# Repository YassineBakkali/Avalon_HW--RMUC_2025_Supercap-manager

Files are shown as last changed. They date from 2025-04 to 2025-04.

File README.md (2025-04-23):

# Avalon - A supercapacitor power manager 

**Avalon** is the custom-designed supercapacitor power manager developed by the **Calibur Robotics team at the National University of Singapore (NUS)** for the **RoboMaster University Championship 2025 (RMUC)**.

This repository contains the full KiCad design files for the Avalon PCB, along with exported schematics and layout PDFs for easier reference and review. Avalon is built to manage high-speed charge and discharge cycles between the robot’s main power source and a dedicated supercapacitor bank.

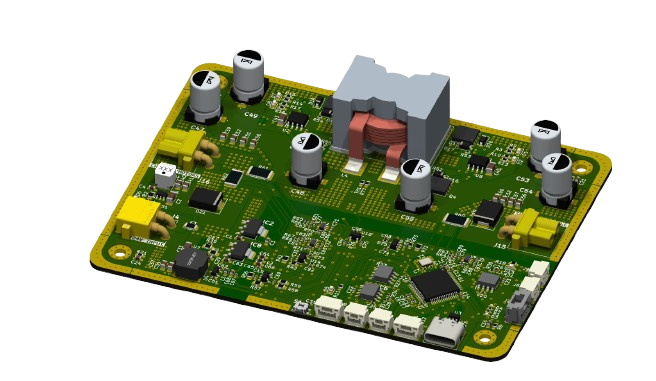
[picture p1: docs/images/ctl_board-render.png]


## Overview

In the RoboMaster competitions, robots must obey strict power limits enforced by the referee system -- typicallycapping the power that can be drawn by the chassis motors at any time. However, short bursts of movement like sprints, collisions, or sudden maneuvers demand far more power than the allowed continuous limit. This creates a mismatch between what the robot can legally draw and what it momentarily needs.

This supercapacitor charger board acts as an intelligent power managemennt module that bridges that gap. By interfacing between the robot's power input (PMM) and supercapacitor bank, it performs real-time charge and discharge cycles to absorb excess power when available and release it when needed. This board thus allow us to perform faster an more agressive movement without breaking power rules.

## How It Works

- During low-power moments (idle, cruise), the board charges the supercaps using leftover headroom from the legal power budget
- When power spikes (e.g. assuming a 24V input, 5A+ with a 60W limit), the board discharges stored energy into the chassis to supplment the robot's main power supply.
- A bidirectional synchronous buck-boost converter, controlled by an STM32G4 microcontroller, enables saemless switching between charge and discharge modes.
- A **high-frequency PID-controlled feedback loop** regulates power transfer at around ~150kHz, ensuring safe and efficient operation.

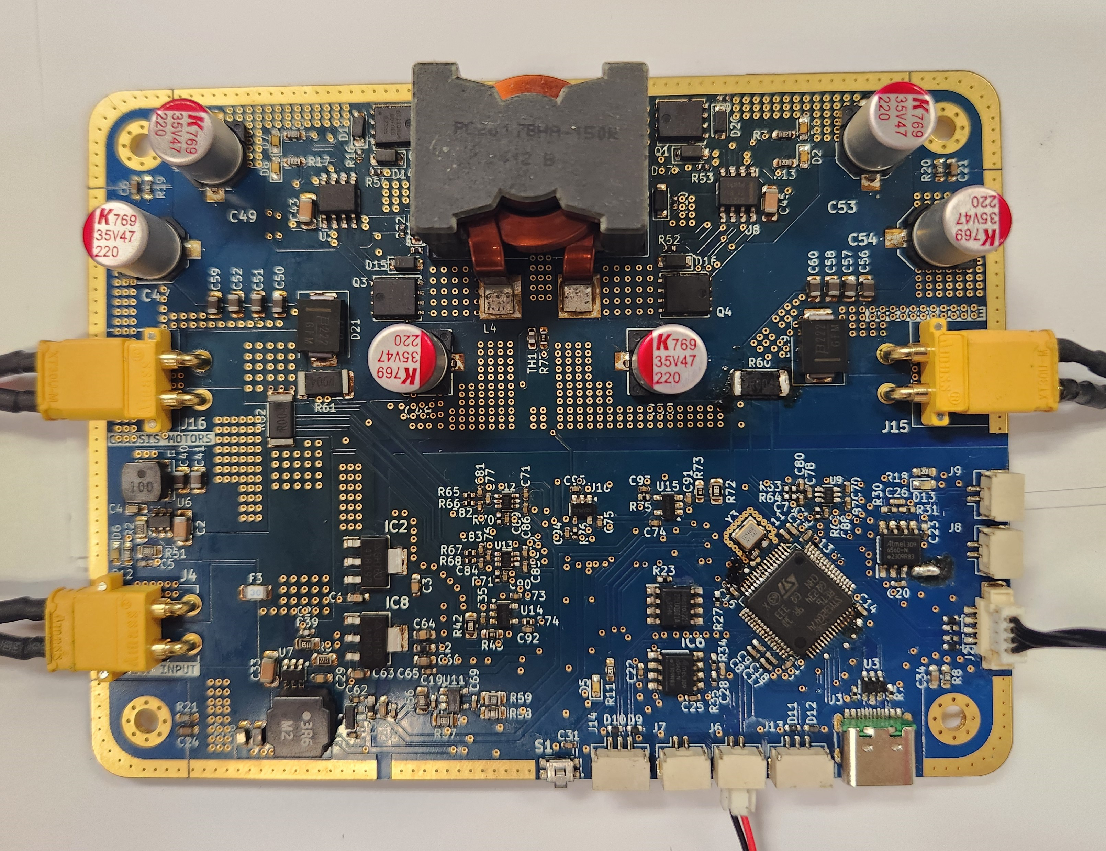
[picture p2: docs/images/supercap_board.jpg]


## Schematics

The full schematics are included as a multi-page PDF [here](pdf/ctl_board.pdf).  
Each sheet is organized by subsystem:

- **Page 1**: Overview / hierarchical design
- **Page 2**: STM32G4 microcontroller and peripherals
- **Page 3**: Power supply regulation, analog references
- **Page 4**: CAN/UART communication interfaces
- **Page 6**: Miscellaneous
- **Page 7**: Main power path and buck-boost gate drivers, current/voltage sensing

Most are clearly labeled, and analog, power, and digital domains are kept well isolated.

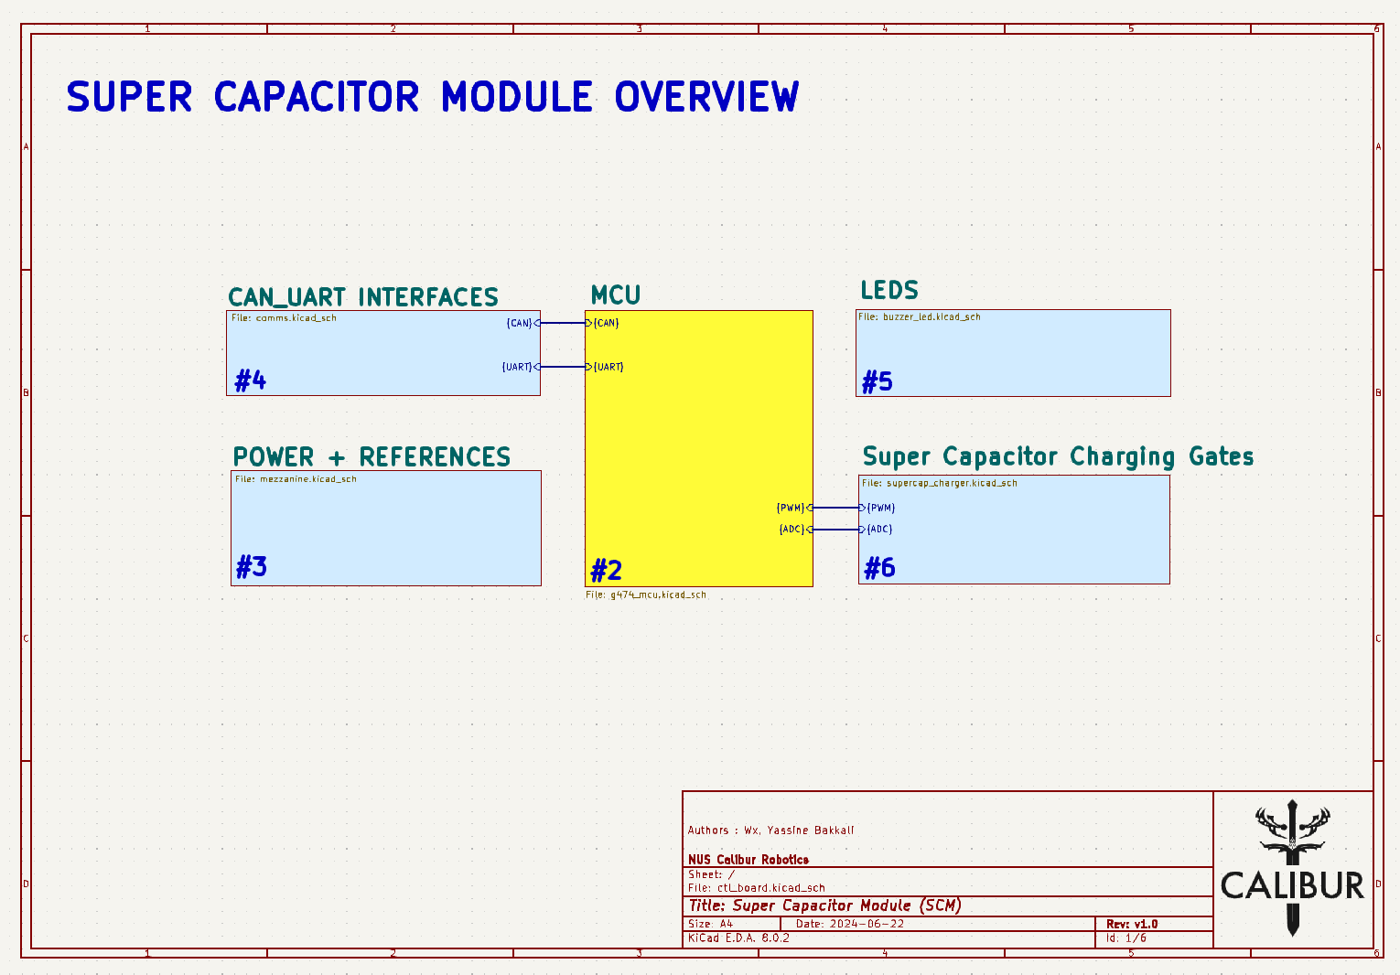
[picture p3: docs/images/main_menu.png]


## Wiring

The diagram below shows how Avalon is integrated into the robot's power system. It connects between the PMM (referee power module) via J4 and the supercapacitor bank via J15, and communicates with the main control board via CAN. All connectors follow our team's internal wiring standard to ensure compatibility across subsystems.

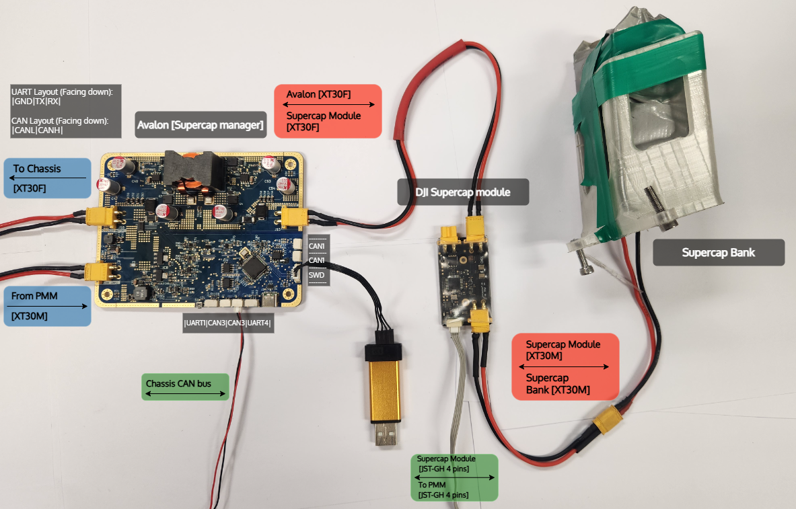
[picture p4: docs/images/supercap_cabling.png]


### Connector Pinout

| Connector | Type | Function |
|---|---|---|
| J4 | XT30PW-M | Input from PMM |
| J15 | XT30PW-F | Output to supercapacitor bank |
| J16 | XT30PW-F | Output to chassis |
| J15 | JST GH 4P | SWD for programming |
| J8 | JST GH 2P | CAN(FD)1 communication |
| J9 | JST GH 2P | CAN(FD)1 communication |
| J6 | JST GH 2P | CAN(FD)3 communication |
| J7 | JST GH 2P | CAN(FD)3 communication |
| J13 | JST GH 4P | UART4 communication |
| J14 | JST GH 4P | UART4 communication |
| J3 | USB-C | USB-FS communication |

## Design choices

This board follows a mixed-signal design, combining high-power switching and analog sensing, so a certain care was taken to physically separate the analog and digital domains. The power section, which includes the buck-boost stage and high-current paths, is isolated from the control logic and signal processing areas to prevent noise from contaminating ADC readings.

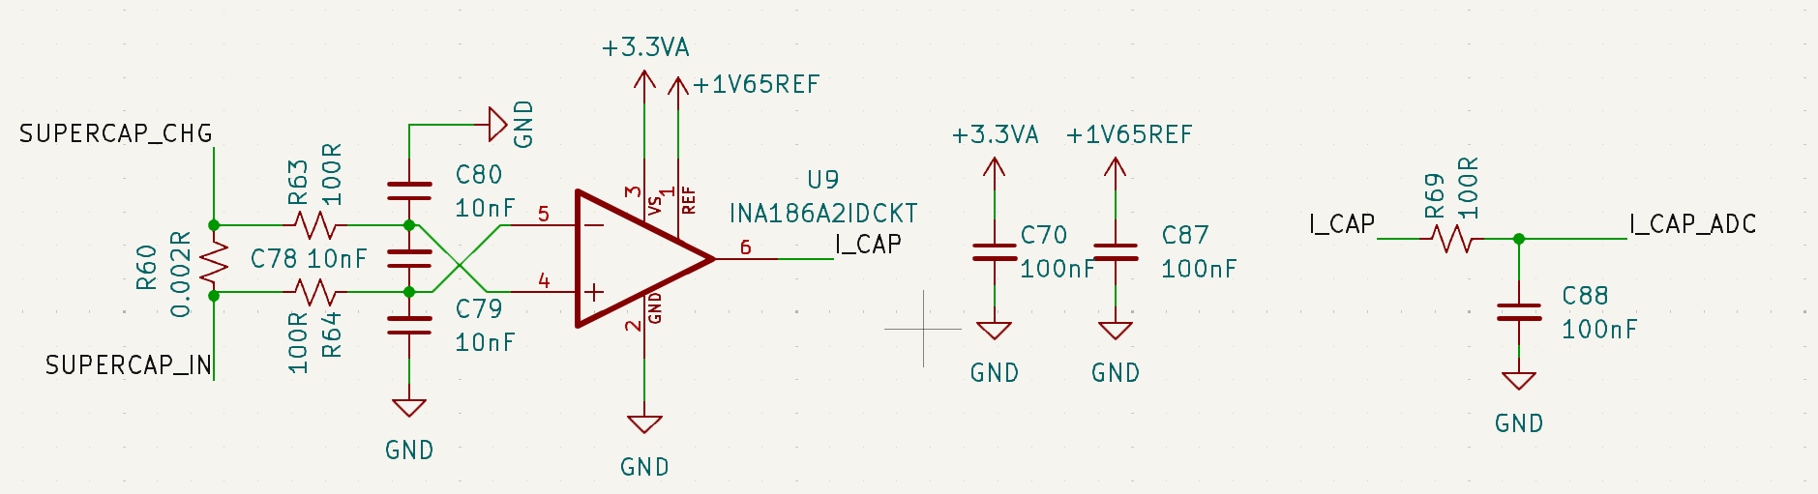
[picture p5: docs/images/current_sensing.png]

*This figure serves as an example of the current sensing circuit used for this board*

To ensure clean current measurements from both the A and B gates of the buck-boost converter as well as the input current, dedicated analog filtering stages were used. Each **INA186** current aplfier is paired with a symmtrical RC filter (100Ω + 10nF) on both inputs, followed by additional bypass capacitors and low-pass filtering before reaching the ADC.

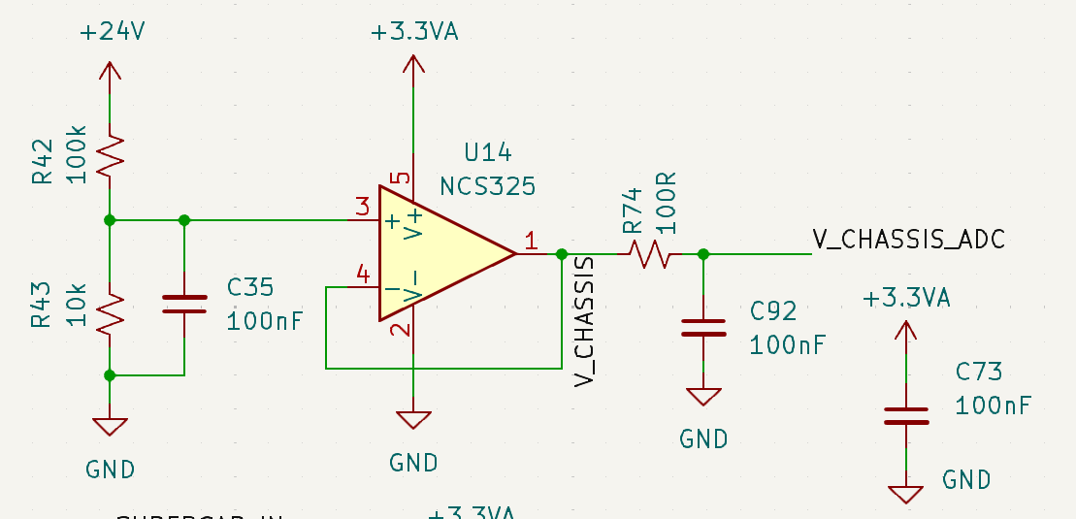
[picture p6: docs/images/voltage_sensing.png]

*This figure serves as an example of the voltage sensing circuit used for this board*

In addition to current sensing, voltage measurements (including temperature sensing) are routed through NCS325 OpAmps in a voltage follower configuration (unity gain) with additional RC filtering on both input and output. 

Driving the power stage is an **STM32G474RETx**, chosen specifically for its **HRTIM (High-Resolution Timer)** peripheral. This allows for extremely fine PWM control at high freqencies, which is ideal for safely switching the four NMOS of our buck-boost circuit.
HRTIMs support edad-time insertion and complementary gate control, which are ssential for avoiding shoot-through in the half-bridges and for achieving reliable control at high frequencies.

Connector selection was made with system integration in mind. We stuck to the standard JST GH, and XT30 connectors already used throughout the robot platform. This keeps the board plug-and-play with existing harnesses and avoids unnecessary cable splicing or custom adapters during deployment. 

Thermally, the board is **clearly** overengineered -- 2oz copper on the surface layers, dense thermal via placement, and wie power pours ensure minimal self-heating. In fact, even under sustained 15A+ operation, thermal tests showed satisfactory temperature rise, making on the onboard temperature sesnor effectively redundant. Stil, it's included and routed with the same analog filtering as voltage signals.

## Bill of Materials (BOM)

The BOM was optimized to balance price and availability. Power-side components such as MOSFETs, gate drivers or the STM32 microcontroller were sourced from **Taobao**, while control-side parts like some analog ICs or passives were sourced from **Digi-Key** for better reliability and availability.

A complete list of components (with reference designators and supplier links) can be found in [`bom/ctl_board.csv`](bom/ctl_board.csv).

## Manufacturing Notes

The board was manufactured by JLCPCB, chosen primarily for its affordability and the ability to handle the required specs without compromise. It supports custom stackups, heavier copper layers, and precise drill tolerances at a very reasonable cost, which made it ideal for this project.

For this design, the following fabrication options were used:

- 4-layer PCB stackup using standard RF-4 substrate
- 2 oz copper weight on surface layers to handle high currents and improve thermal performance
- Thermal vias placed around high-power areas and under high-power components (MOSFET gates) to help transfer heat to internal planes
- Blue soldermask, white silkscreen
- ENIG finish (Mostly for bling)

## License

This hardware design is released under the MIT license.  
See [`LICENSE`](LICENSE) for full terms.

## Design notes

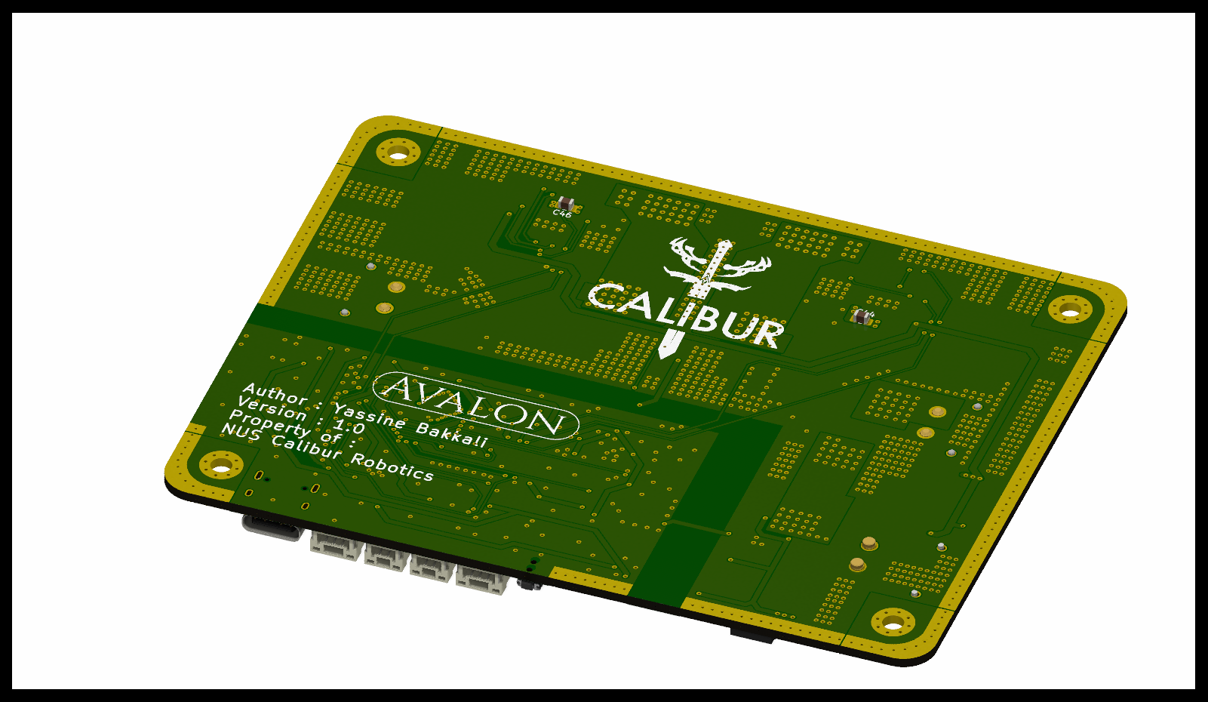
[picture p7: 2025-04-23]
pictures/back_ctl_board.png

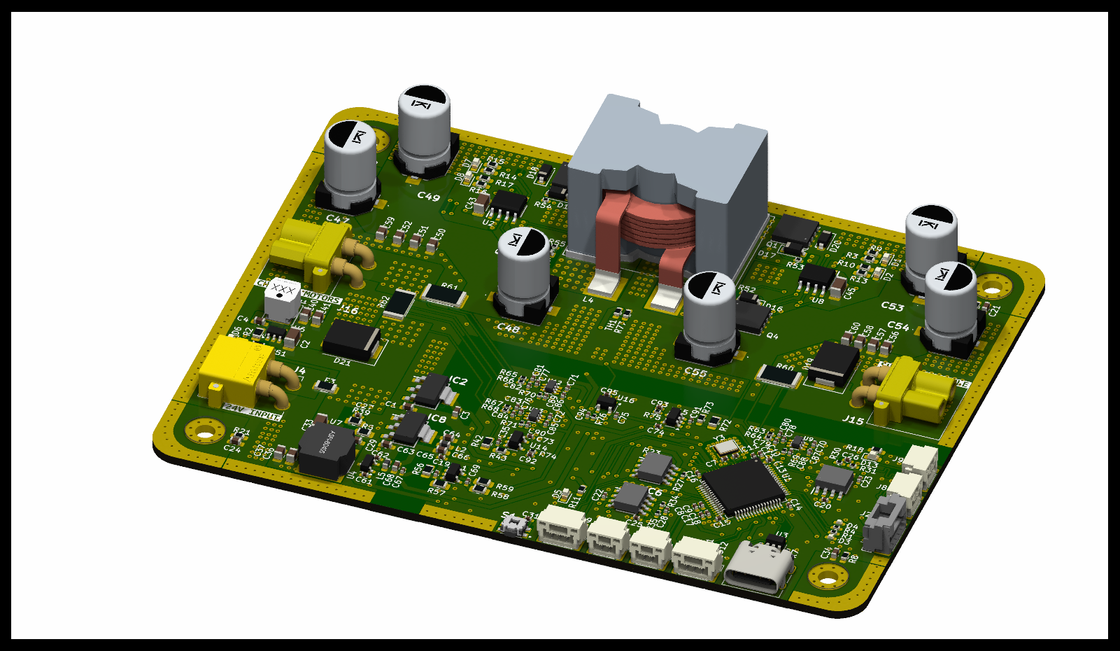
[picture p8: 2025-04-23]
pictures/ctl_board.png

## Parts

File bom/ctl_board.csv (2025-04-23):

Reference | Value | Datasheet | Footprint | Qty | DNP
C1,C43,C45,C63,C66,C68 | 10uF | ~ | -- mixed values -- | 6
C2,C33 | 36v10uF | https://www.digikey.sg/en/products/detail/samsung-electro-mechanics/CL31A106MBHNNNE/5961220 | Capacitor_SMD:C_1206_3216Metric_Pad1.33x1.80mm_HandSolder | 2
C3,C64 | 22uF | ~ | Capacitor_SMD:C_0603_1608Metric_Pad1.08x0.95mm_HandSolder | 2
C4,C29 | 50v100nF | https://www.digikey.sg/en/products/detail/samsung-electro-mechanics/CL10B104KB8NNNC/3886658 | Capacitor_SMD:C_0603_1608Metric_Pad1.08x0.95mm_HandSolder | 2
C5,C27 | 50v100pF | https://www.digikey.sg/en/products/detail/yageo/CC0402KRX7R9BB101/2833584 | Capacitor_SMD:C_0402_1005Metric_Pad0.74x0.62mm_HandSolder | 2
C6,C21,C24,C34 | 1000nF | ~ | Capacitor_SMD:C_0603_1608Metric_Pad1.08x0.95mm_HandSolder | 4
C7,C11 | 12pF | ~ | Capacitor_SMD:C_0402_1005Metric | 2
C8,C12,C13,C14,C15,C16,C19,C20,C22,C23,C25,C31,C35,C44,C46,C61,C62,C65,C67,C69,C70,C71,C72,C73,C74,C75,C85,C86,C87,C91,C95 | 100nF | ~ | -- mixed values -- | 31
C9,C18 | 1uF | ~ | Capacitor_SMD:C_0402_1005Metric_Pad0.74x0.62mm_HandSolder | 2
C10 | 4.7uF | ~ | Capacitor_SMD:C_0402_1005Metric_Pad0.74x0.62mm_HandSolder | 1
C17,C76,C77,C78,C79,C80,C81,C82,C83,C84 | 10nF | ~ | -- mixed values -- | 10
C26,C28 | 4.7nF | ~ | Capacitor_SMD:C_0402_1005Metric_Pad0.74x0.62mm_HandSolder | 2
C36,C37,C40,C41 | 50v22uF | https://www.digikey.sg/en/products/detail/samsung-electro-mechanics/CL21A226MAYNNNE/10479857 | Capacitor_SMD:C_0805_2012Metric_Pad1.18x1.45mm_HandSolder | 4
C47,C48,C49,C53,C54,C55 | 220uF@35V | https://www.digikey.sg/en/products/detail/kemet/A769KS227M1VLAS016/16162576 | footprints:A769KS227M1VLAS016 | 6
C50,C51,C52,C56,C57,C58,C59,C60 | 20uF@50V | https://www.digikey.sg/en/products/detail/tdk-corporation/C2012X5R1V226M125AC/3951664 | Capacitor_SMD:C_0805_2012Metric_Pad1.18x1.45mm_HandSolder | 8
C88,C89,C90,C92,C93,C94 | 0.1uF | ~ | Capacitor_SMD:C_0402_1005Metric | 6
D1,D2,D5,D6,D7,D8,D13 | LED | ~ | LED_SMD:LED_0603_1608Metric_Pad1.05x0.95mm_HandSolder | 7
D3,D4,D9,D10,D11,D12 | TPD1E10B06DPYR-EV | https://assets.nexperia.com/documents/data-sheet/PESD5V0F1BL.pdf | Diode_SMD:D_0402_1005Metric_Pad0.77x0.64mm_HandSolder | 6
D14,D15,D16,D17 | MMSD4148T3G | https://www.digikey.sg/en/products/detail/onsemi/MMSD4148T3G/1482130 | Diode_SMD:D_SOD-123 | 4
D18,D20 | BAT41ZFILM | https://www.digikey.sg/en/products/detail/stmicroelectronics/BAT41ZFILM/1207025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 | Diode_SMD:D_SOD-123 | 2
D19,D21 | SMCJ33A | https://www.digikey.sg/en/products/detail/bourns-inc/SMCJ33A/2254641 | Diode_SMD:D_SMC | 2
F3 | 0685H9300-01 | https://www.digikey.sg/en/products/detail/bel-fuse-inc/0685H9300-01/5466710 | Fuse:Fuse_1206_3216Metric | 1
H1,H2,H3,H9 | MountingHole_Pad | ~ | MountingHole:MountingHole_3.2mm_M3_Pad_Via | 4
IC2,IC8 | AZ1117CH-3.3TRG1 | https://datasheet.datasheetarchive.com/originals/distributors/Datasheets-DGA25/1776204.pdf | SamacSys_Parts:SOT230P700X180-4N | 2
IC3 | AT25EU0021A-SSHN-T | https://www.renesas.com/us/en/products/memory-logic/non-volatile-memory/spi-nor-flash/dual-quad-spi-memory/at25eu0021a-2mbit-ultra-low-energy-serial-flash-mem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 | SOIC127P600X175-8N | 1
IC4,IC6 | ATA6560-GAQW-N |  | SamacSys_Parts:SOIC127P600X175-8N | 2
J2 | MOLEX_ClikMate | ~ | Connector_Molex:Molex_CLIK-Mate_502386-0470_1x04-1MP_P1.25mm_Horizontal | 1
J3 | USB_C_Receptacle_USB2.0 | https://www.usb.org/sites/default/files/documents/usb_type-c.zip | Connector_USB:USB_C_Receptacle_HRO_TYPE-C-31-M-12 | 1
J4 | XT30PW | https://www.tme.eu/Document/4acc913878197f8c2e30d4b8cdc47230/XT30UPB%20SPEC.pdf | SamacSys_Parts:XT30PWM | 1
J6,J7,J8,J9 | JST_GH_SM02 | ~ | Connector_JST:JST_GH_SM02B-GHS-TB_1x02-1MP_P1.25mm_Horizontal | 4
J13,J14 | JST_GH_SM03 | ~ | Connector_JST:JST_GH_SM03B-GHS-TB_1x03-1MP_P1.25mm_Horizontal | 2
J15,J16 | XT30PW-F | https://www.tme.eu/Document/ce4077e36b79046da520ca73227e15de/XT30PW%20SPEC.pdf | SamacSys_Parts:XT30PWF | 2
L1 | 10.0uH | https://www.digikey.sg/en/products/detail/tdk-corporation/VLS5045EX-100M/5286674 | footprints:IND_VLS5045EX-100M | 1
L2,L5 | 26R@100MHz | https://www.digikey.sg/en/products/detail/murata-electronics/BLM18KG260TN1D/1982760 | Inductor_SMD:L_0603_1608Metric_Pad1.05x0.95mm_HandSolder | 2
L3 | 3.6uH | https://www.digikey.sg/en/products/detail/taiyo-yuden/LSXNH8080YBL3R6NJG/16667411 | footprints:IND_ASPI-6045S-3R6N-T | 1
L4 | 15uH | https://www.bourns.com/docs/Product-Datasheets/PQ2617.pdf | footprints:IND_SUPERCAP | 1
Q1,Q2,Q3,Q4 | POW_NMOS | https://www.digikey.sg/en/products/detail/goford-semiconductor/GT095N04D5/21183376 | footprints:DFN5&asterisk_6-8L_GFD | 4
R1,R4,R63,R64,R65,R66,R67,R68,R69,R70,R71,R74,R75,R76 | 100R | ~ | -- mixed values -- | 14
R2,R5 | 22.1k | https://www.digikey.sg/en/products/detail/stackpole-electronics-inc/RMCF0805FT22K1/1760211 | Resistor_SMD:R_0805_2012Metric_Pad1.20x1.40mm_HandSolder | 2
R3,R12,R13,R15,R17,R58 | 1k | ~ | -- mixed values -- | 6
R6,R7 | 5.1kR | ~ | Resistor_SMD:R_0402_1005Metric_Pad0.72x0.64mm_HandSolder | 2
R8,R19,R20,R21 | 1M | ~ | Resistor_SMD:R_0603_1608Metric_Pad0.98x0.95mm_HandSolder | 4
R9,R10,R14,R16,R43,R73,R77 | 10k | ~ | Resistor_SMD:R_0603_1608Metric_Pad0.98x0.95mm_HandSolder | 7
R11,R18 | 200R | ~ | Resistor_SMD:R_0603_1608Metric_Pad0.98x0.95mm_HandSolder | 2
R23,R27 | 4.7k | ~ | Resistor_SMD:R_0402_1005Metric_Pad0.72x0.64mm_HandSolder | 2
R30,R31,R34,R35 | 60R | ~ | Resistor_SMD:R_0402_1005Metric_Pad0.72x0.64mm_HandSolder | 4
R39 | 115.8k | https://www.digikey.sg/en/products/detail/yageo/RC0805FR-07115KL/727564 | Resistor_SMD:R_0805_2012Metric_Pad1.20x1.40mm_HandSolder | 1
R42,R56,R57,R72 | 100k | ~ | Resistor_SMD:R_0805_2012Metric_Pad1.20x1.40mm_HandSolder | 4
R51 | 309.0k | ~ | Resistor_SMD:R_0805_2012Metric_Pad1.20x1.40mm_HandSolder | 1
R52,R53,R54,R55 | 1R | ~ | Resistor_SMD:R_0402_1005Metric | 4
R59 | 33R | ~ | Resistor_SMD:R_0805_2012Metric_Pad1.20x1.40mm_HandSolder | 1
R60,R61,R62 | 0.002R | ~ | Resistor_SMD:R_2512_6332Metric | 3
S1 | EVQP7C01P | https://www.arrow.com/en/products/evqp7c01p/panasonic | SamacSys_Parts:EVQP7C01P | 1
TH1 | NTC 10K | ~ | Resistor_SMD:R_0603_1608Metric_Pad0.98x0.95mm_HandSolder | 1
U1 | STM32G474RETx | https://www.st.com/resource/en/datasheet/stm32g474re.pdf | Package_QFP:LQFP-64_10x10mm_P0.5mm | 1
U2,U8 | UCC27211AQDDARQ1 | UCC27211AQDDARQ1 | footprints:DDA0008E_N | 2
U3 | USBLC6-2SC6 | https://www.st.com/resource/en/datasheet/usblc6-2.pdf | Package_TO_SOT_SMD:SOT-23-6 | 1
U4 | REF3033 | http://www.ti.com/lit/ds/symlink/ref3033.pdf | Package_TO_SOT_SMD:SOT-23 | 1
U6,U7 | AP63200WU | https://www.diodes.com/assets/Datasheets/AP63200-AP63201-AP63203-AP63205.pdf | Package_TO_SOT_SMD:TSOT-23-6 | 2
U9,U12,U13 | INA186A2IDCKT |  | footprints:INA186 | 3
U11,U14,U15,U16 | NCS325 | http://www.onsemi.com/pub/Collateral/NCS325-D.PDF | Package_TO_SOT_SMD:SOT-23-5 | 4
Y3 | ECS-480-8-33B2Q-JVY-TR3 | https://www.digikey.sg/en/products/detail/ecs-inc/ECS-480-8-33B2Q-JVY-TR3/22464855 | Crystal:Crystal_SMD_3225-4Pin_3.2x2.5mm | 1

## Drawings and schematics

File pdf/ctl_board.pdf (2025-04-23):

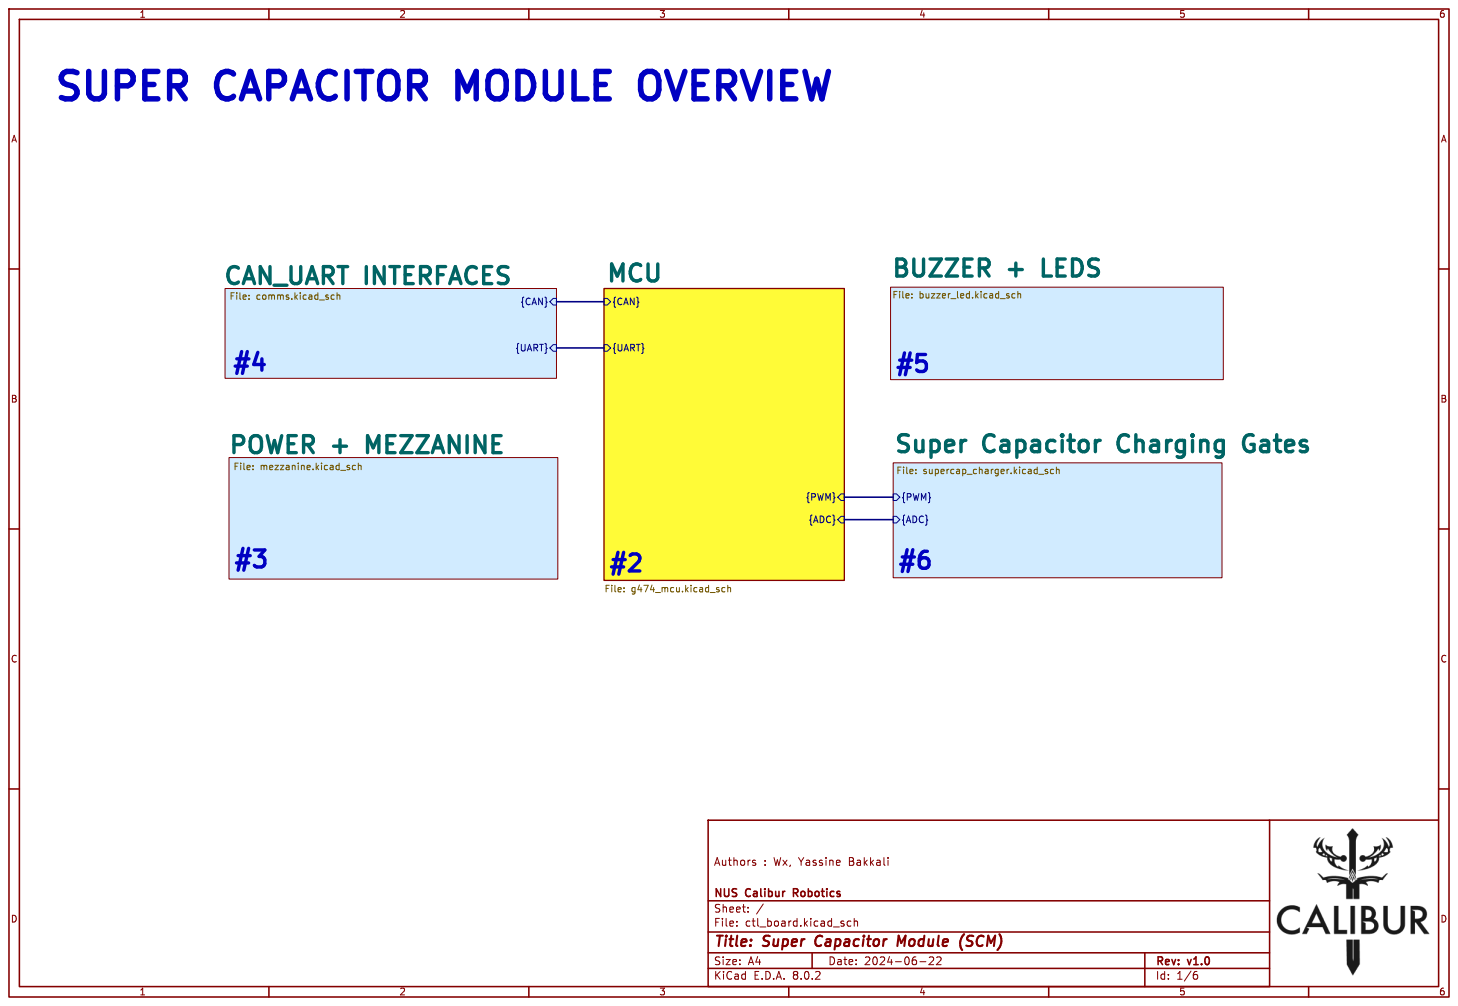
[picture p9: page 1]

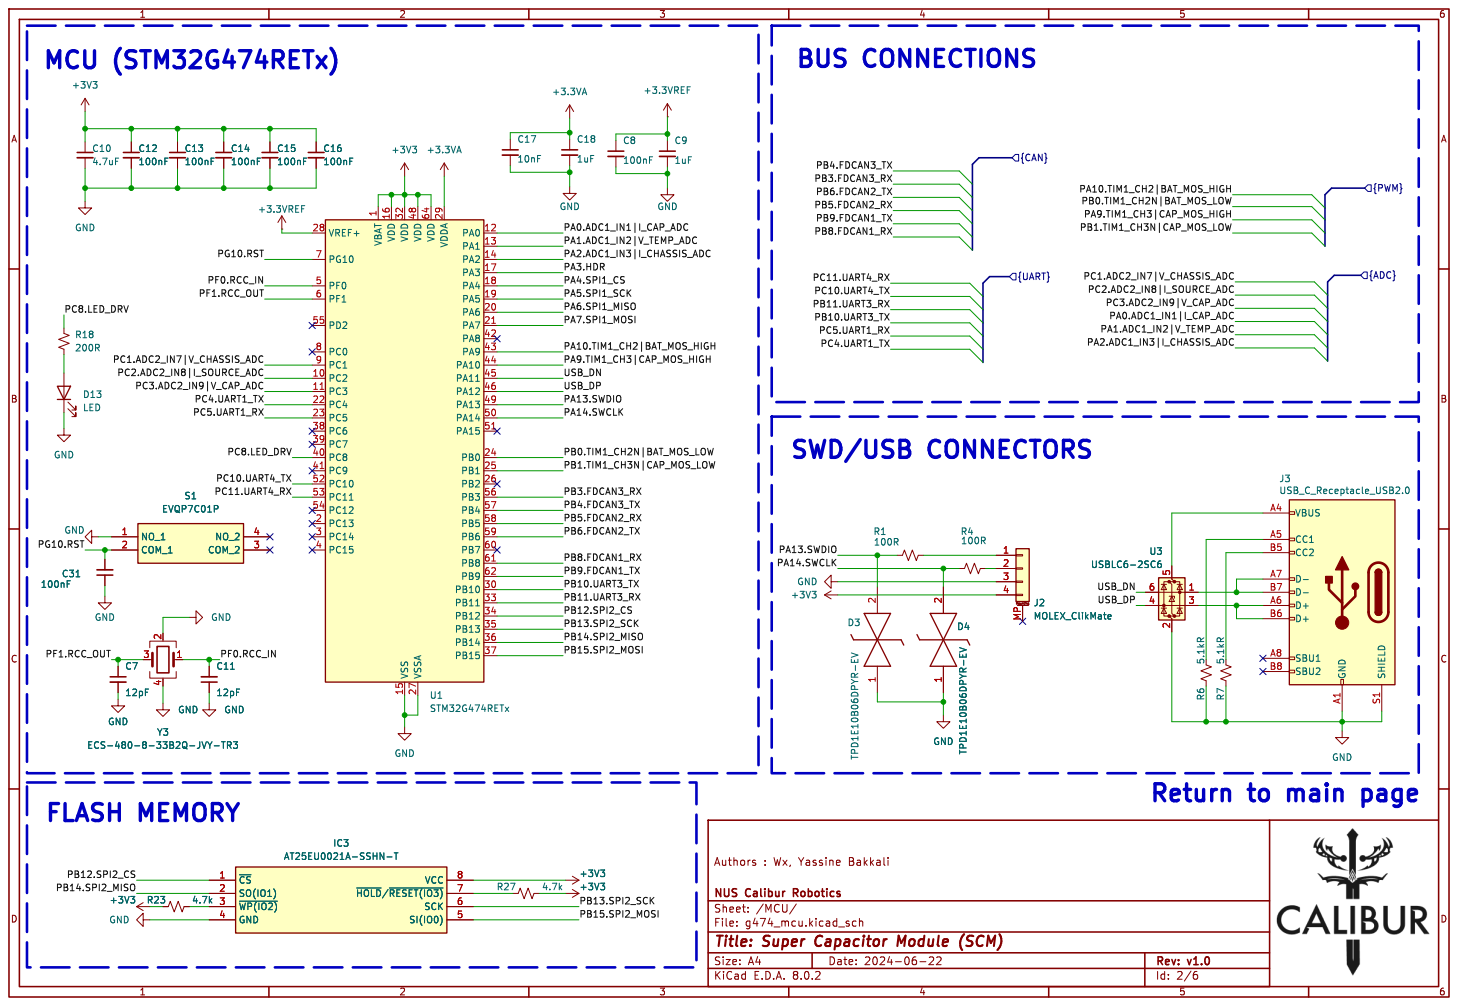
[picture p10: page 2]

1 PC2 10 PC3 11 PA0 12 PA1 13 PA2 14 VSS 15 VDD 16 PA3 17 PA4 18 PA5 19 PC13 2 PA6 20 PA7 21 PC4 22 PC5 23 PB0 24 PB1 25 PB2 26 VSSA 27 VREF+ 28 VDDA 29 PC14 3 PB10 30 VDD 32 PB11 33 PB12 34 PB13 35 PB14 36 PB15 37 PC6 38 PC7 39 PC15 4 PC8 40 PC9 41 PA8 42 PA9 43 PA10 44 PA11 45 PA12 46 VDD 48 PA13 49 PF0 5 PA14 50 PA15 51 PC10 52 PC11 53 PC12 54 PD2 55 PB3 56 PB4 57 PB5 58 PB6 59 PF1 6 PB7 60 PB8 61 PB9 62 VDD 64 PG10 7 PC0 8 PC1 9 U1STM32G474RETx +3V3 GND

4 Y3 ECS-480-8-33B2Q-JVY-TR3 GND GND

Return to main page

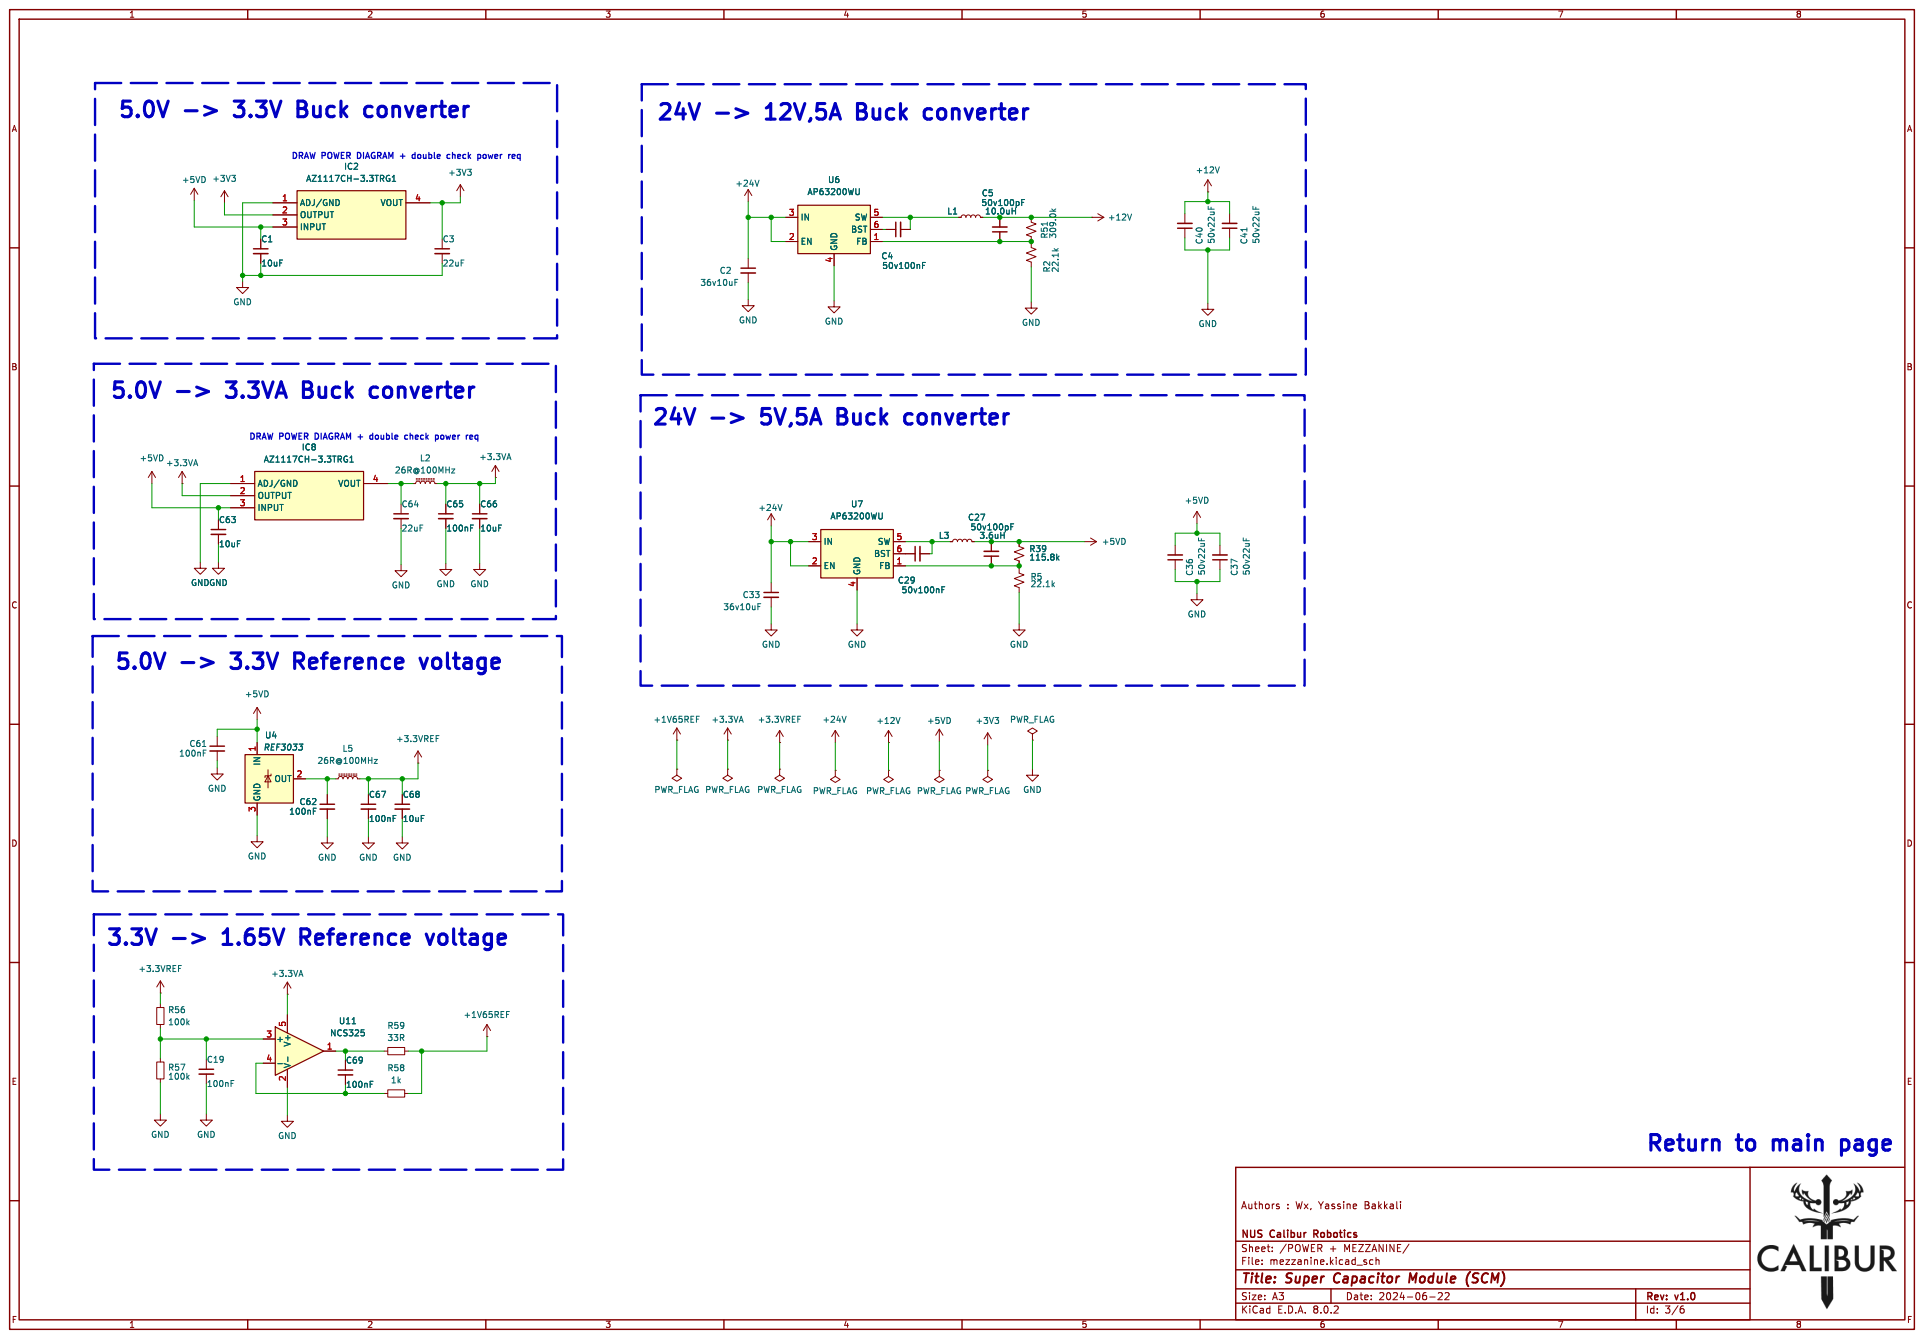
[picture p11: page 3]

DRAW POWER DIAGRAM + double check power req U4 REF3033 IN

Return to main page

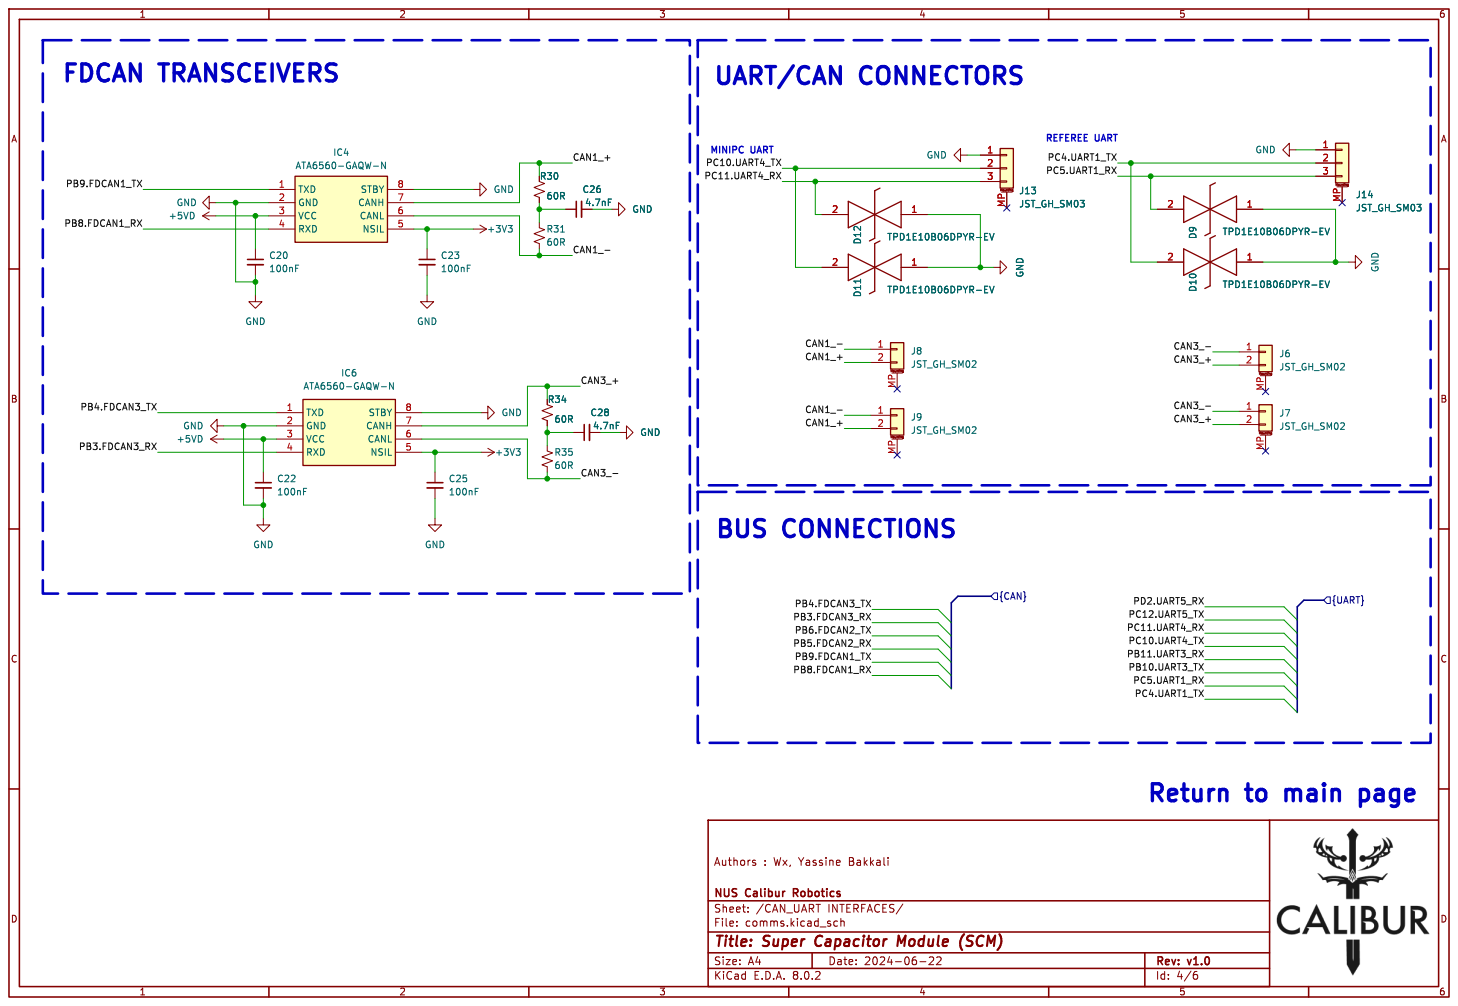
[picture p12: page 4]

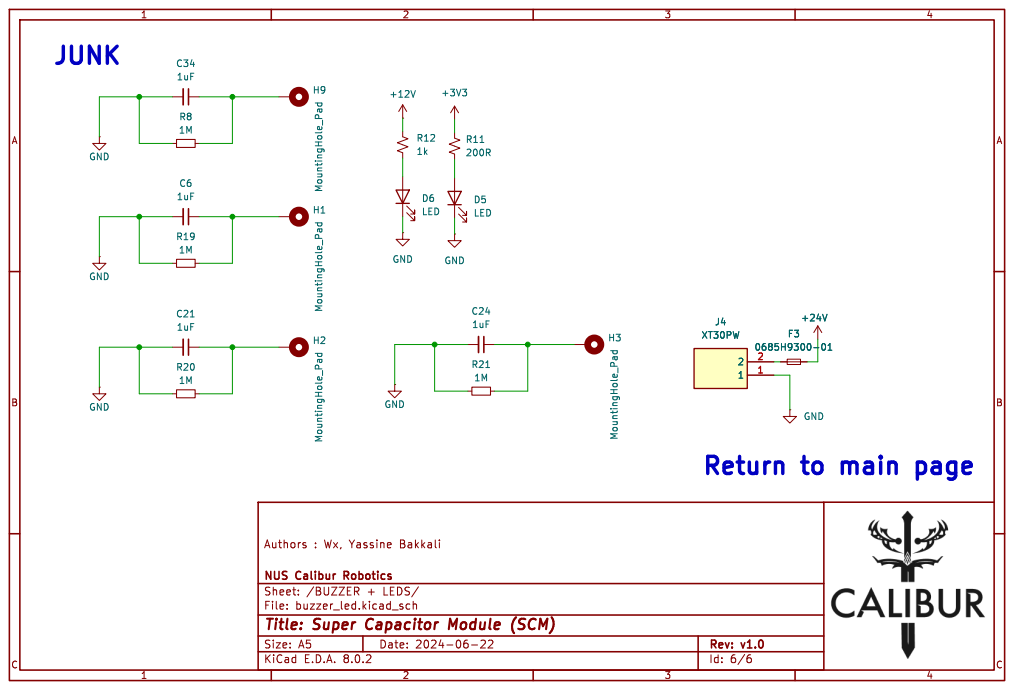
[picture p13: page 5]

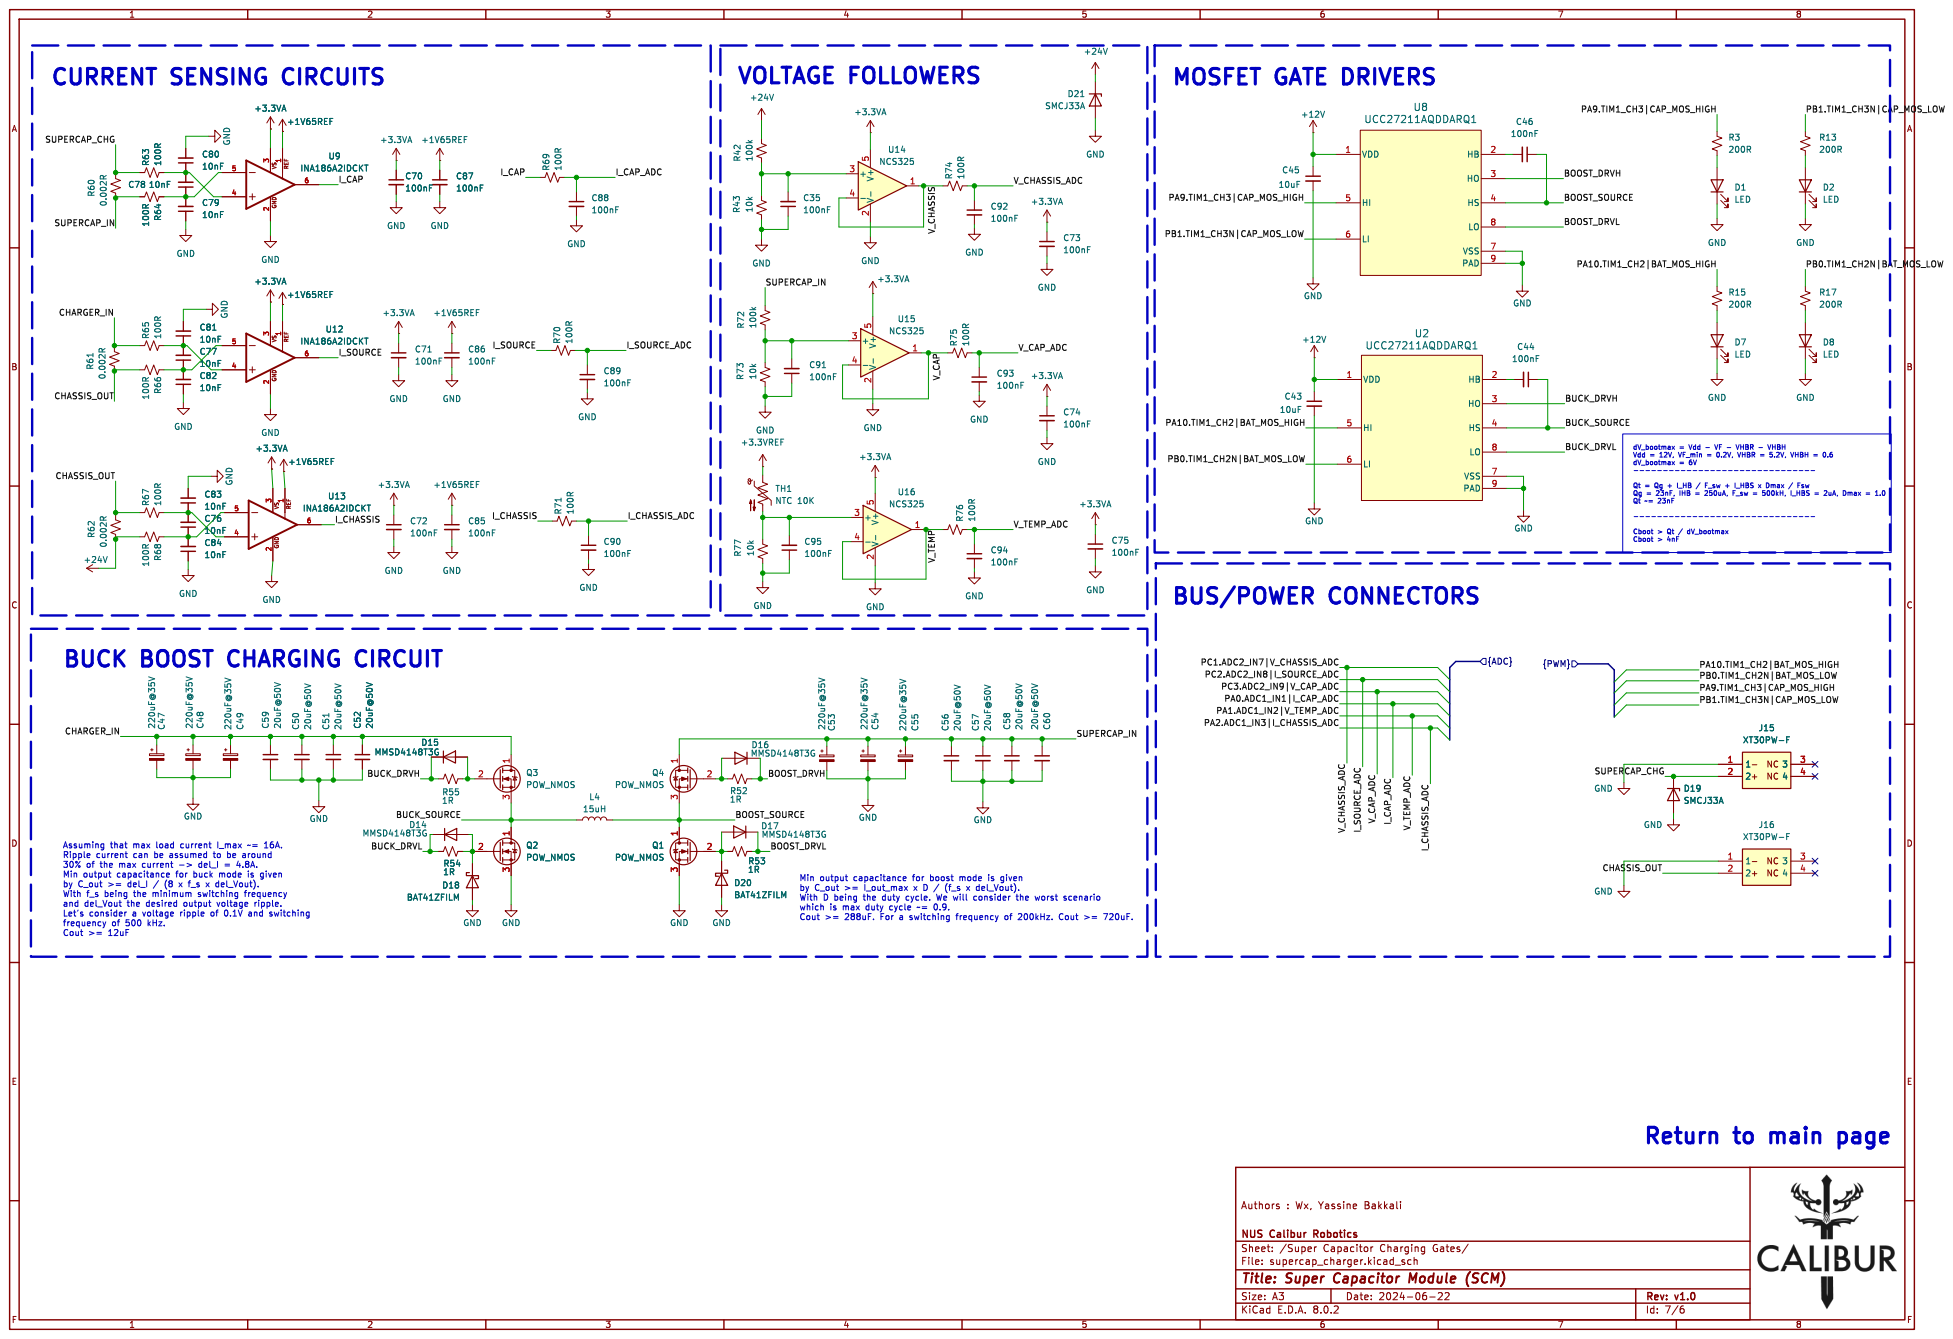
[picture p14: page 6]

dV_bootmax = Vdd - VF - VHBR - VHBH
Vdd = 12V, VF_min = 0.2V, VHBR = 5.2V, VHBH = 0.6 dV_bootmax = 6V

------------------------------- Qt = Qg + I_HB / F_sw + I_HBS x Dmax / Fsw

Qg = 23nF, IHB = 250uA, F_sw = 500kH, I_HBS = 2uA, Dmax = 1.0 Qt ~= 23nF

Assuming that max load current I_max ~= 16A. Ripple current can be assumed to be around

Return to main page

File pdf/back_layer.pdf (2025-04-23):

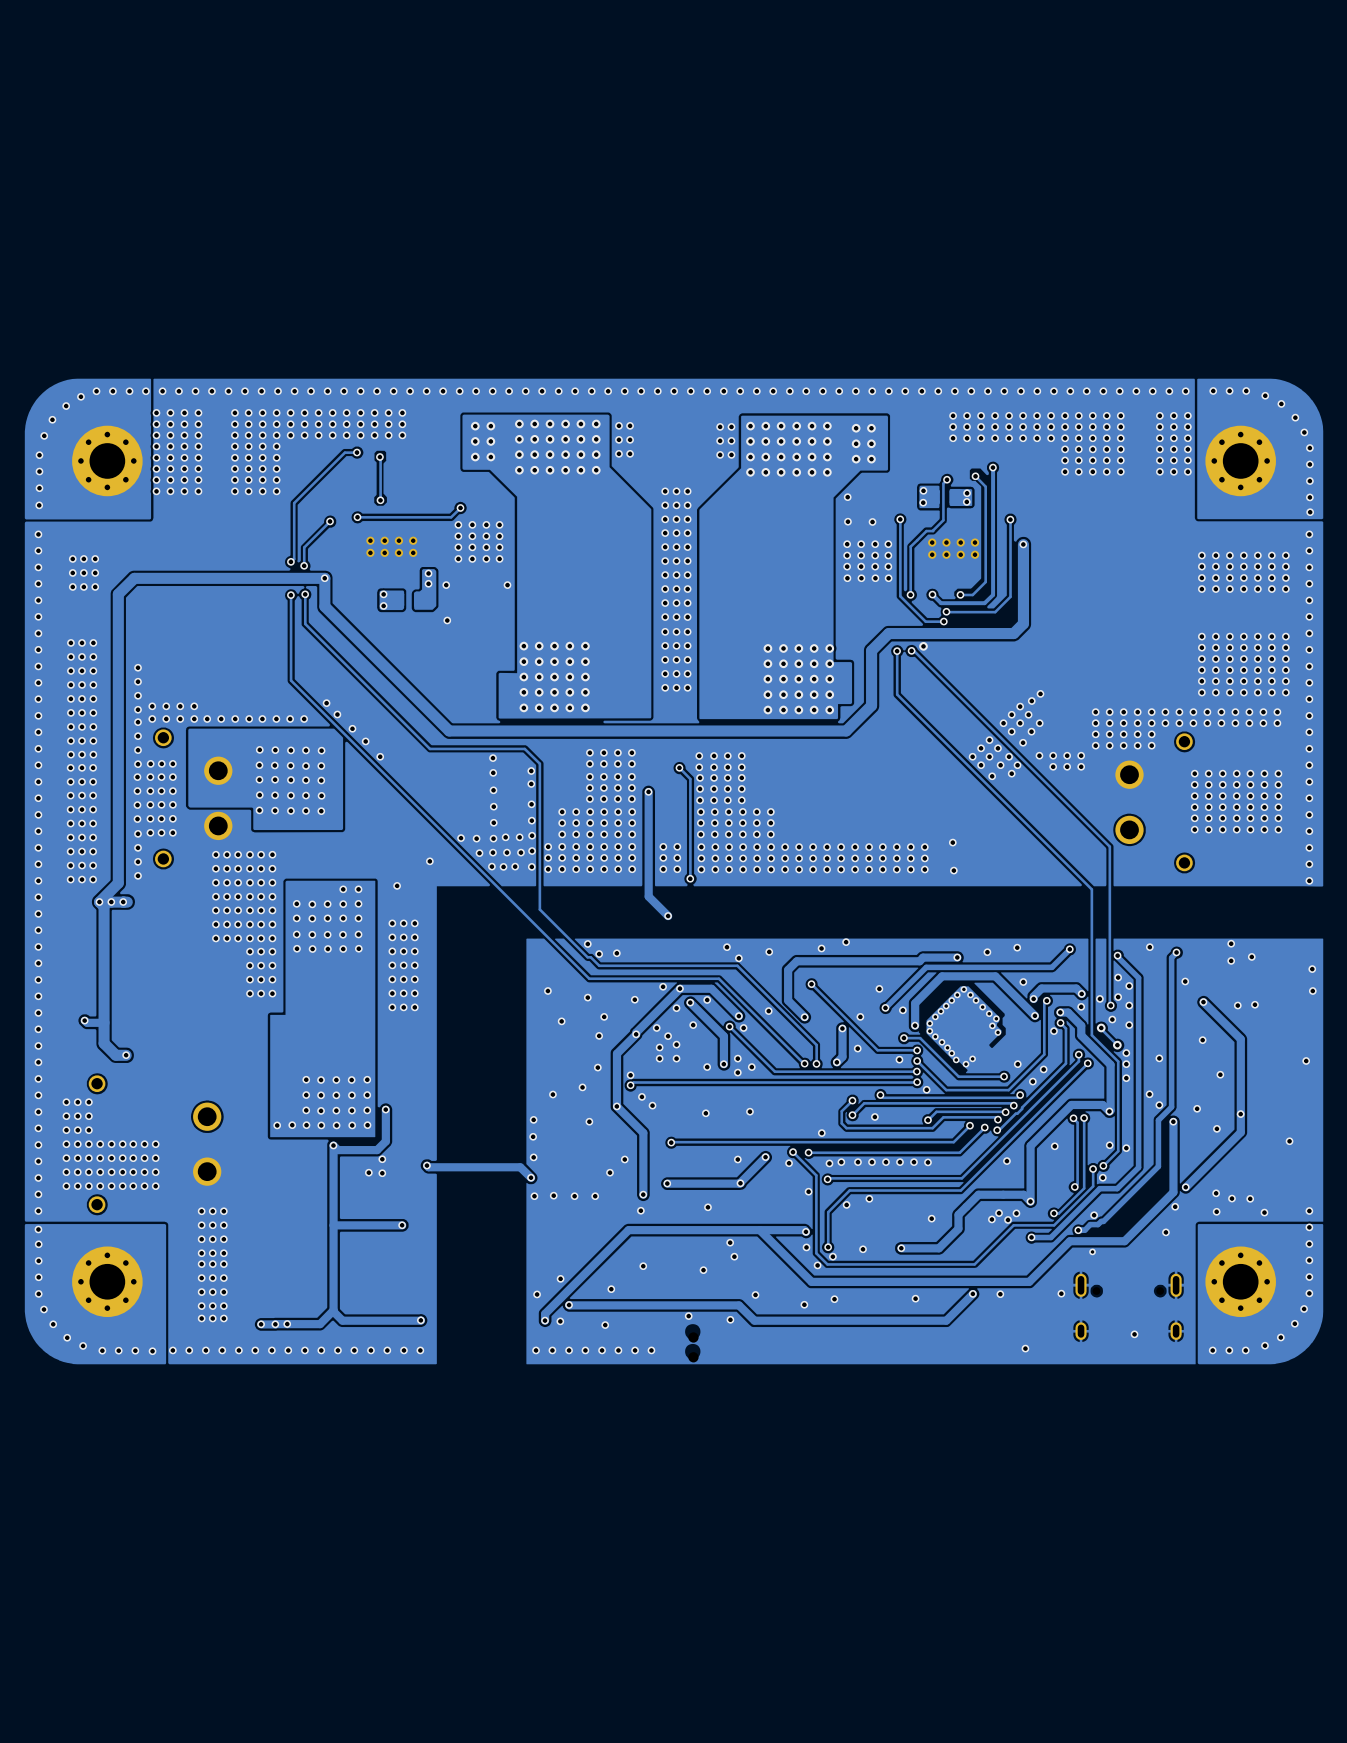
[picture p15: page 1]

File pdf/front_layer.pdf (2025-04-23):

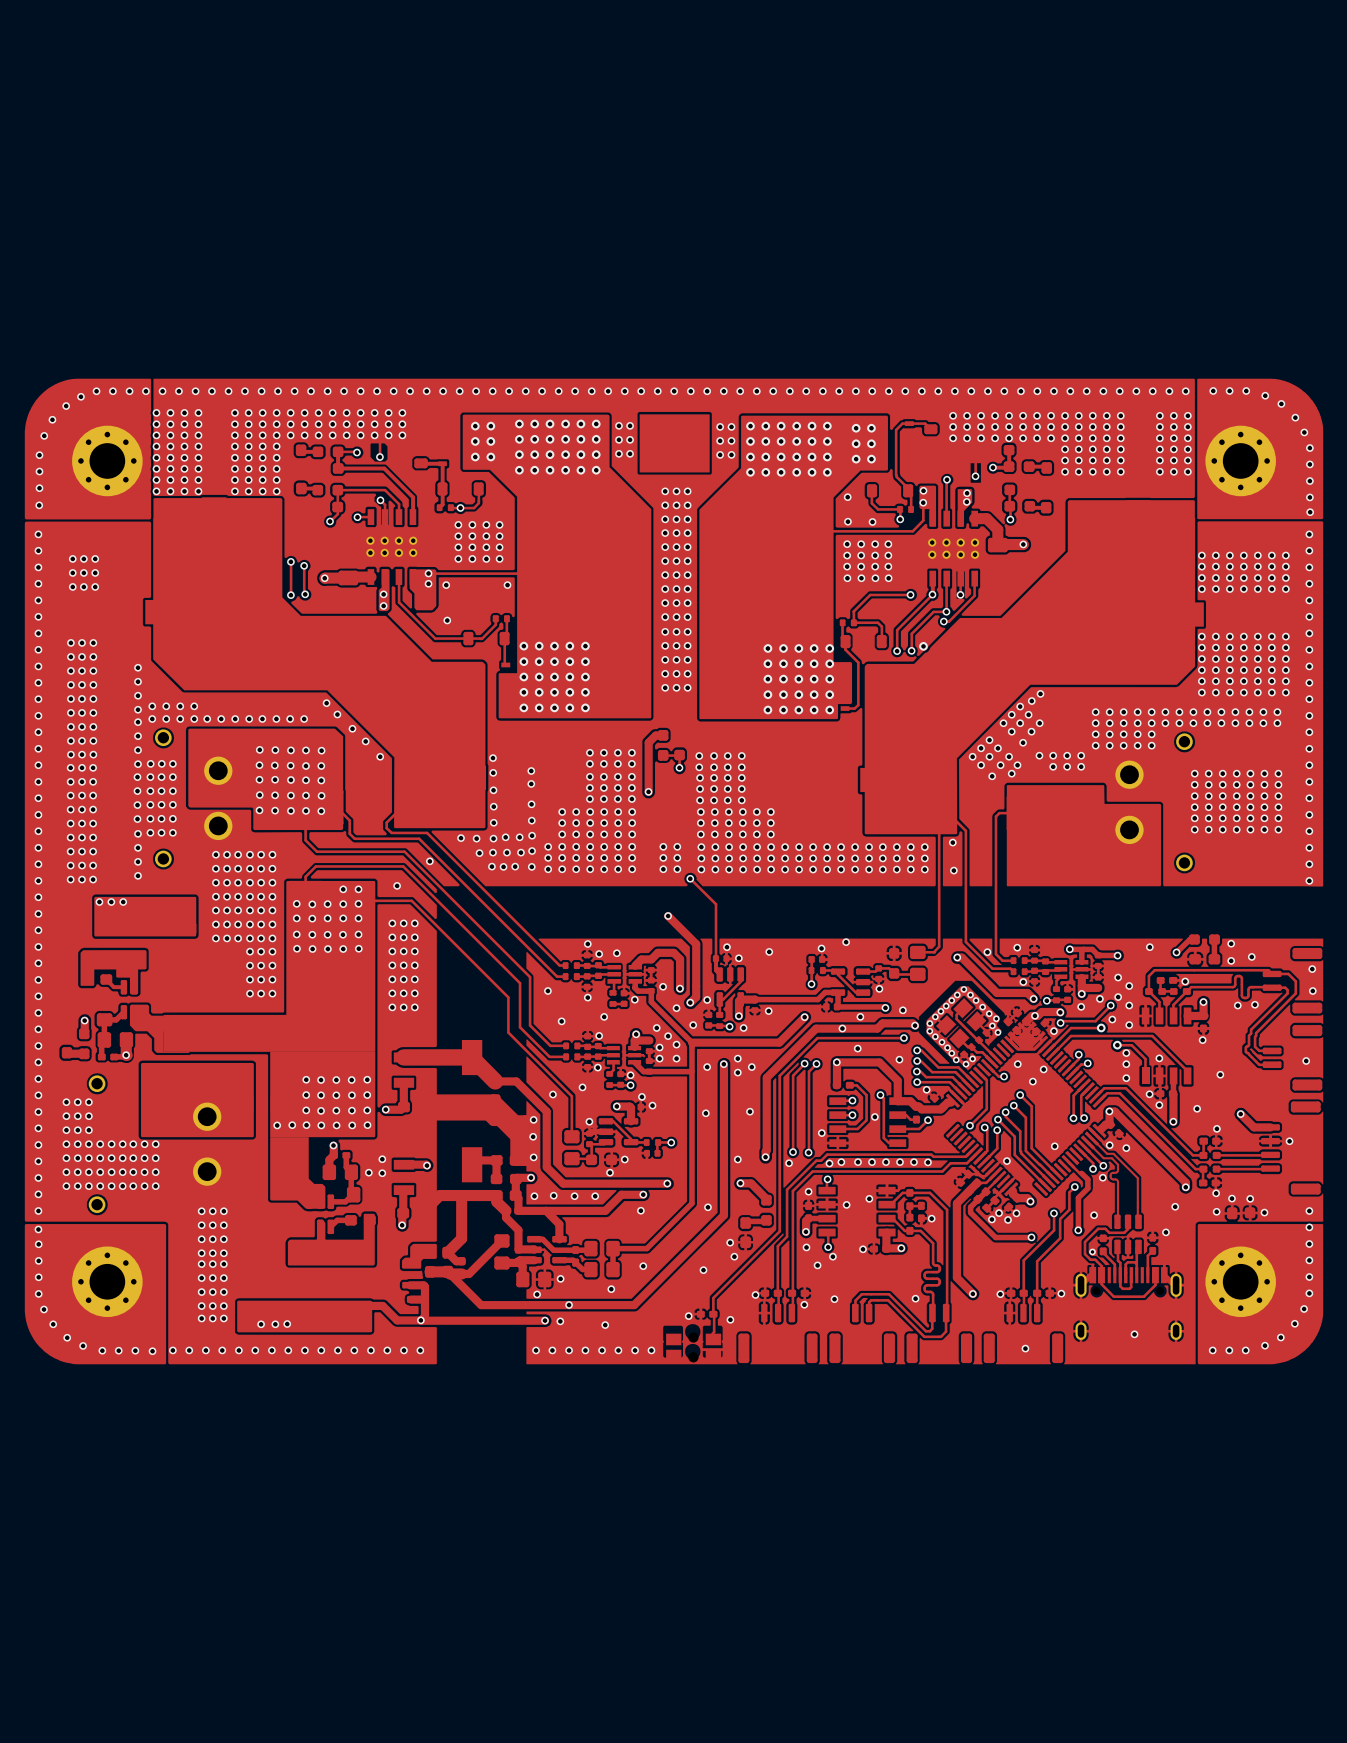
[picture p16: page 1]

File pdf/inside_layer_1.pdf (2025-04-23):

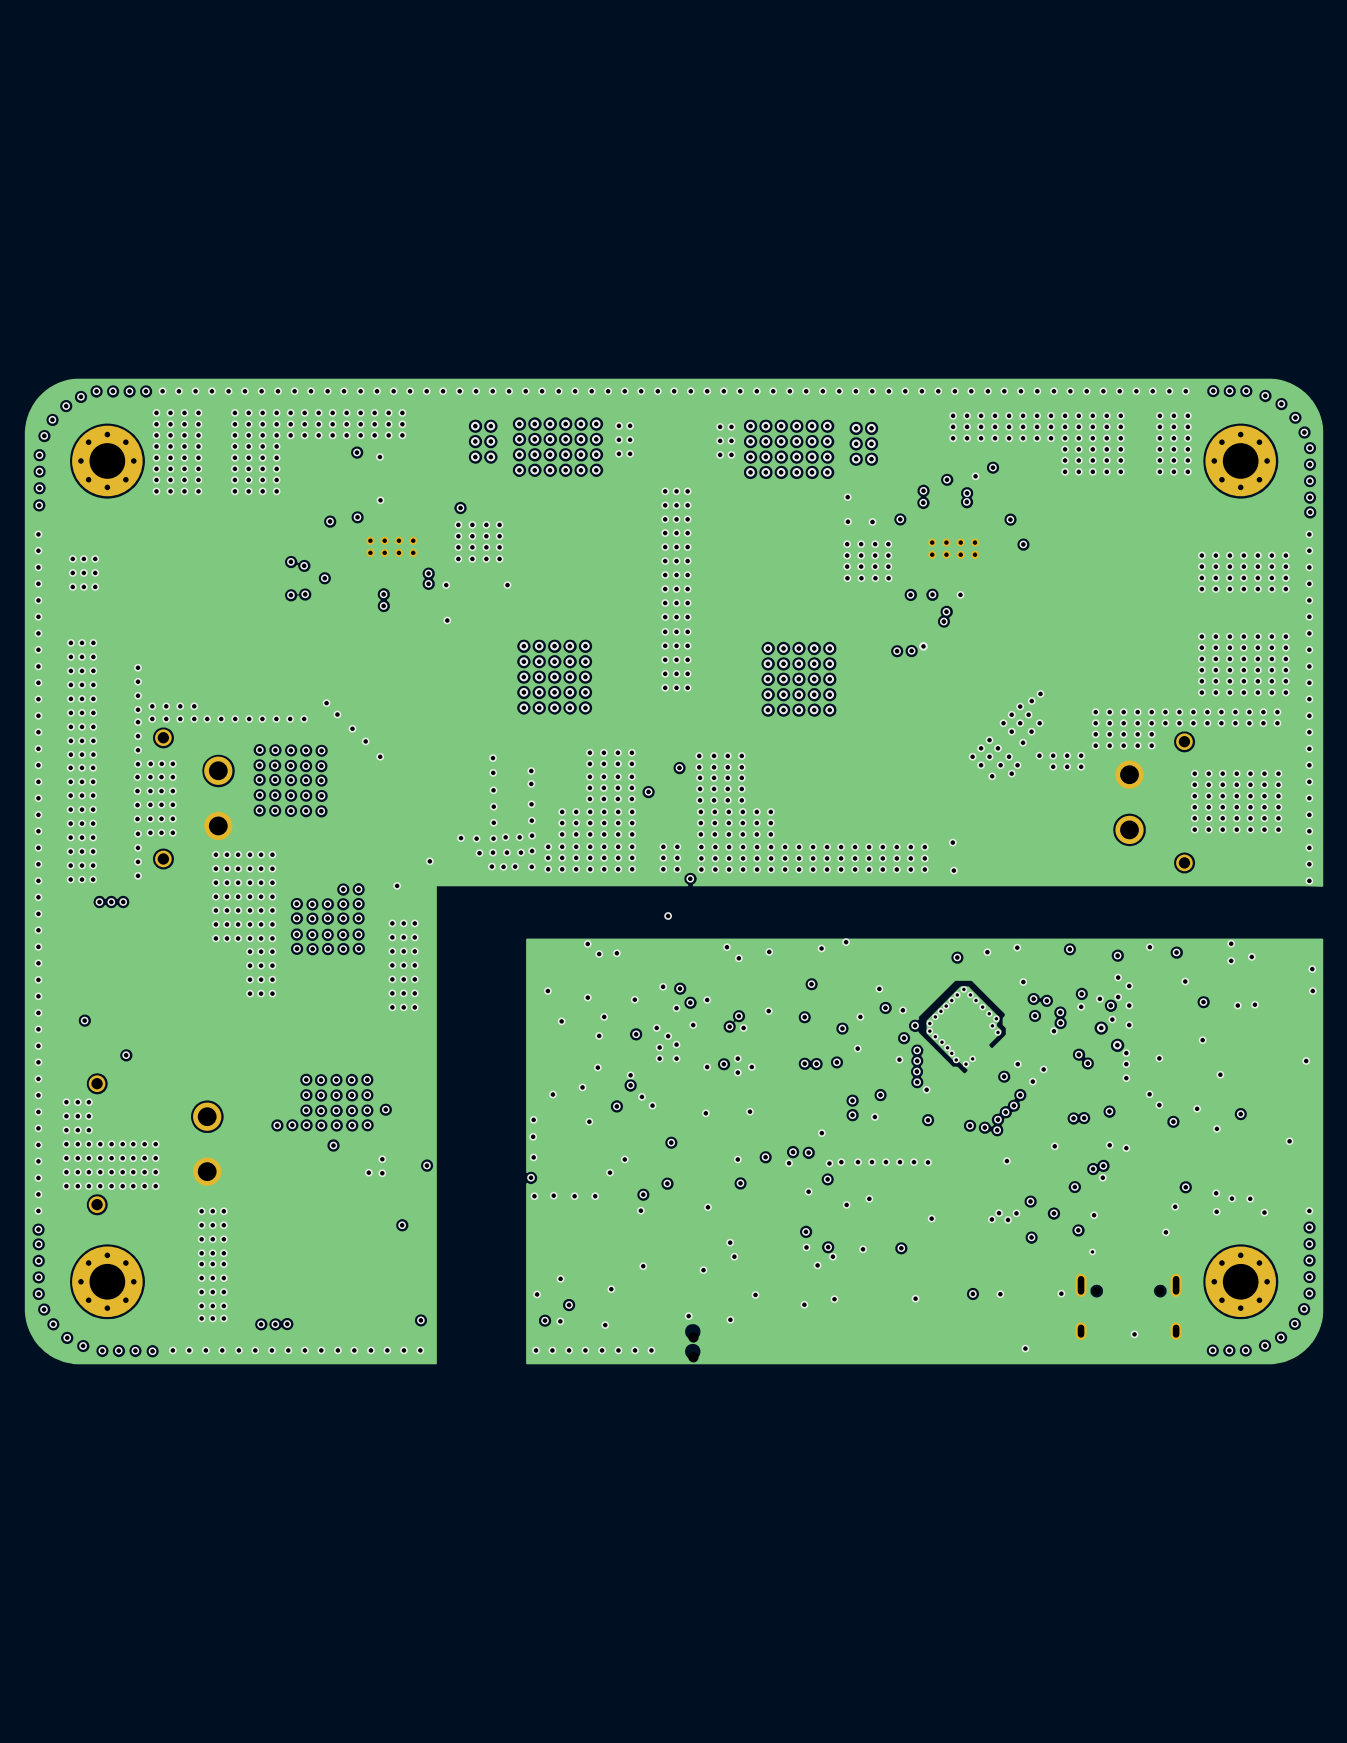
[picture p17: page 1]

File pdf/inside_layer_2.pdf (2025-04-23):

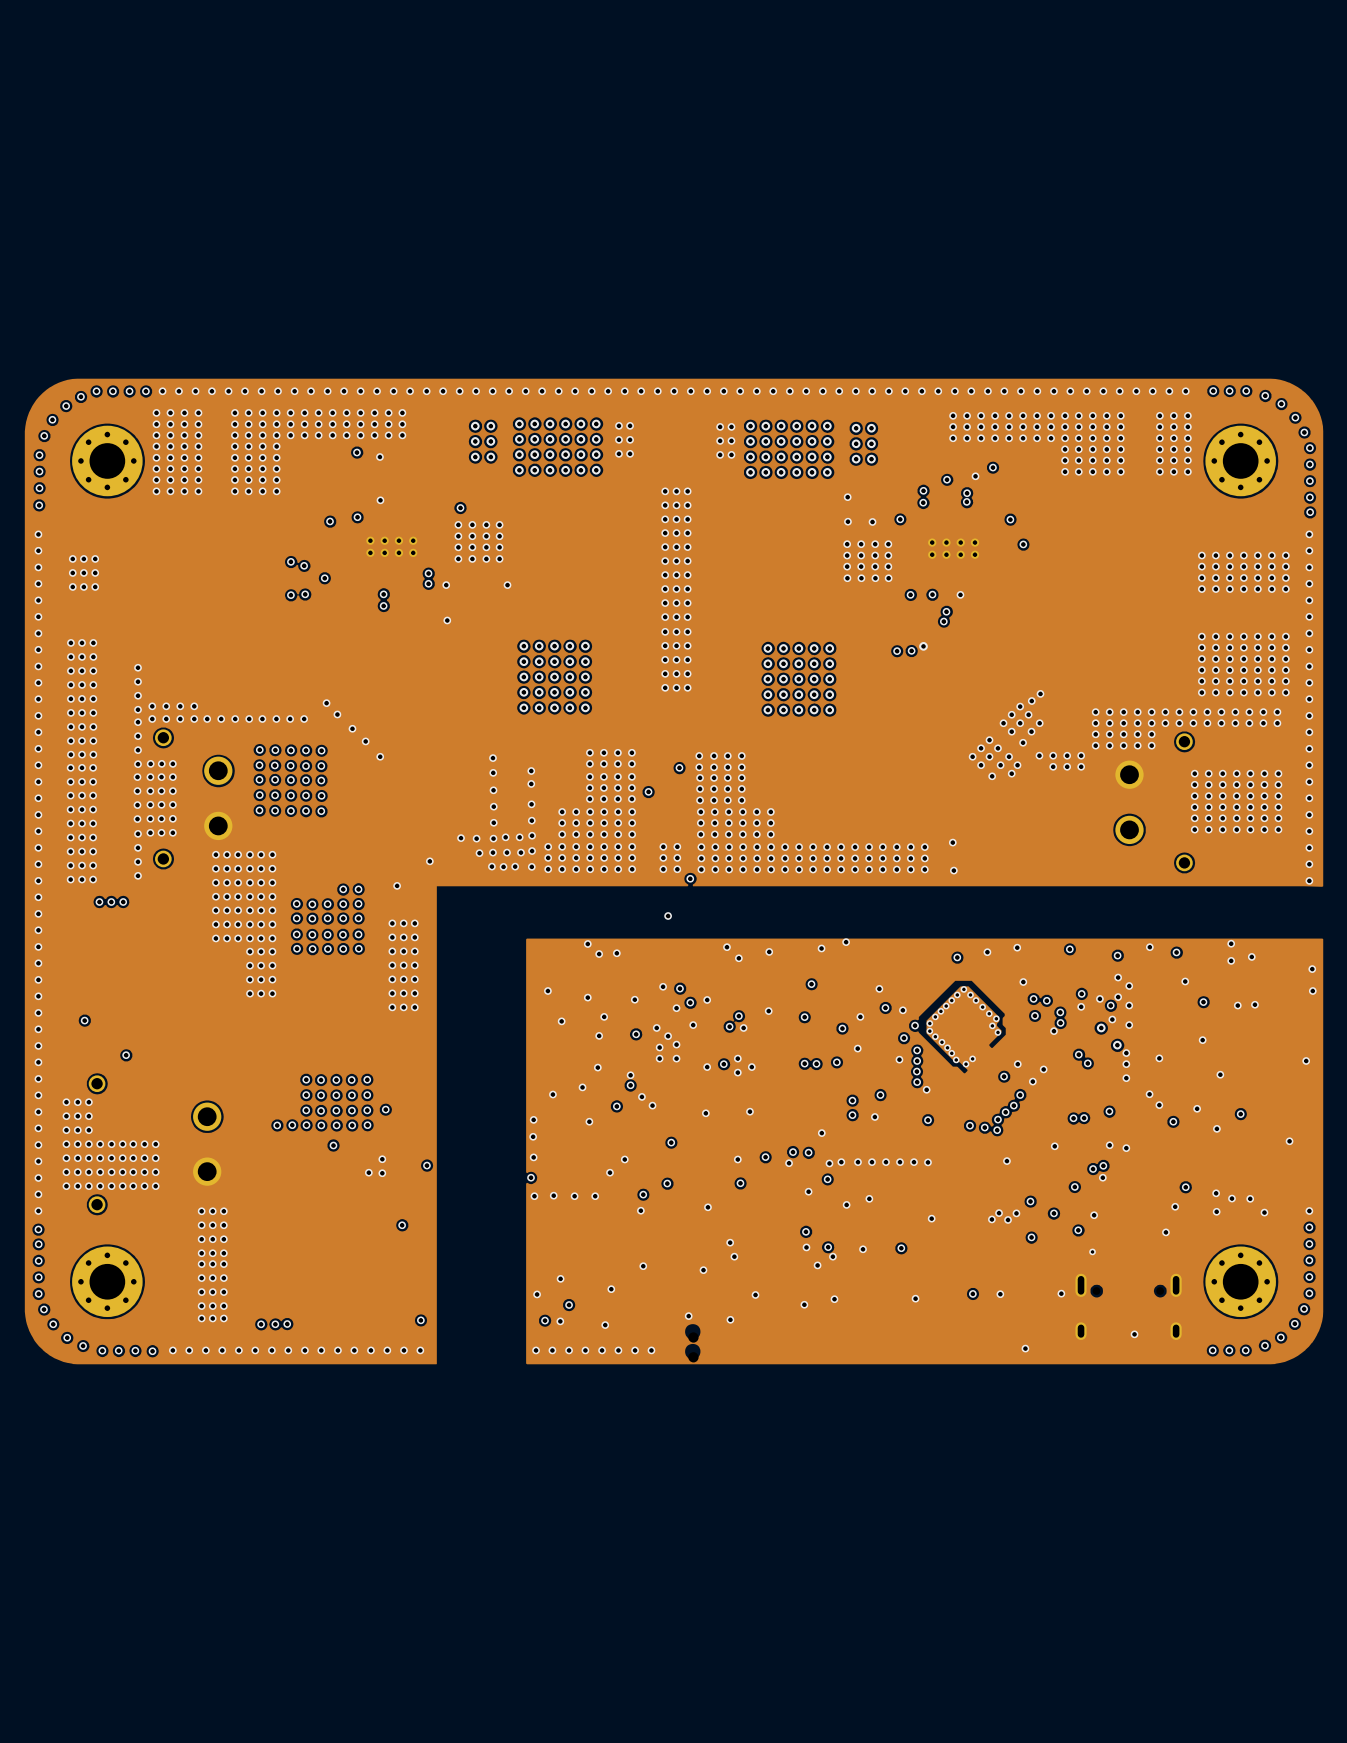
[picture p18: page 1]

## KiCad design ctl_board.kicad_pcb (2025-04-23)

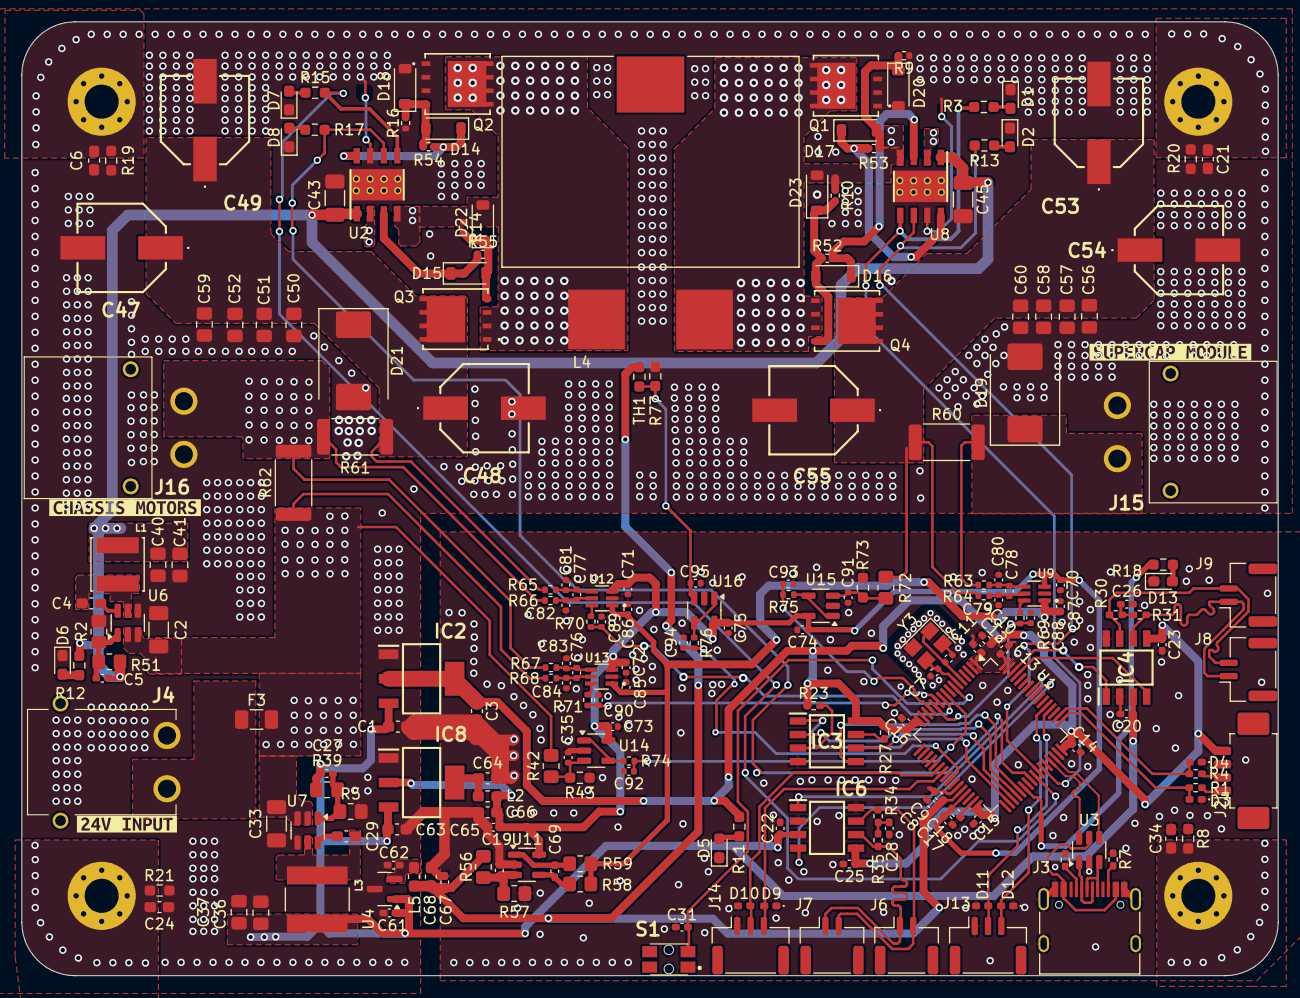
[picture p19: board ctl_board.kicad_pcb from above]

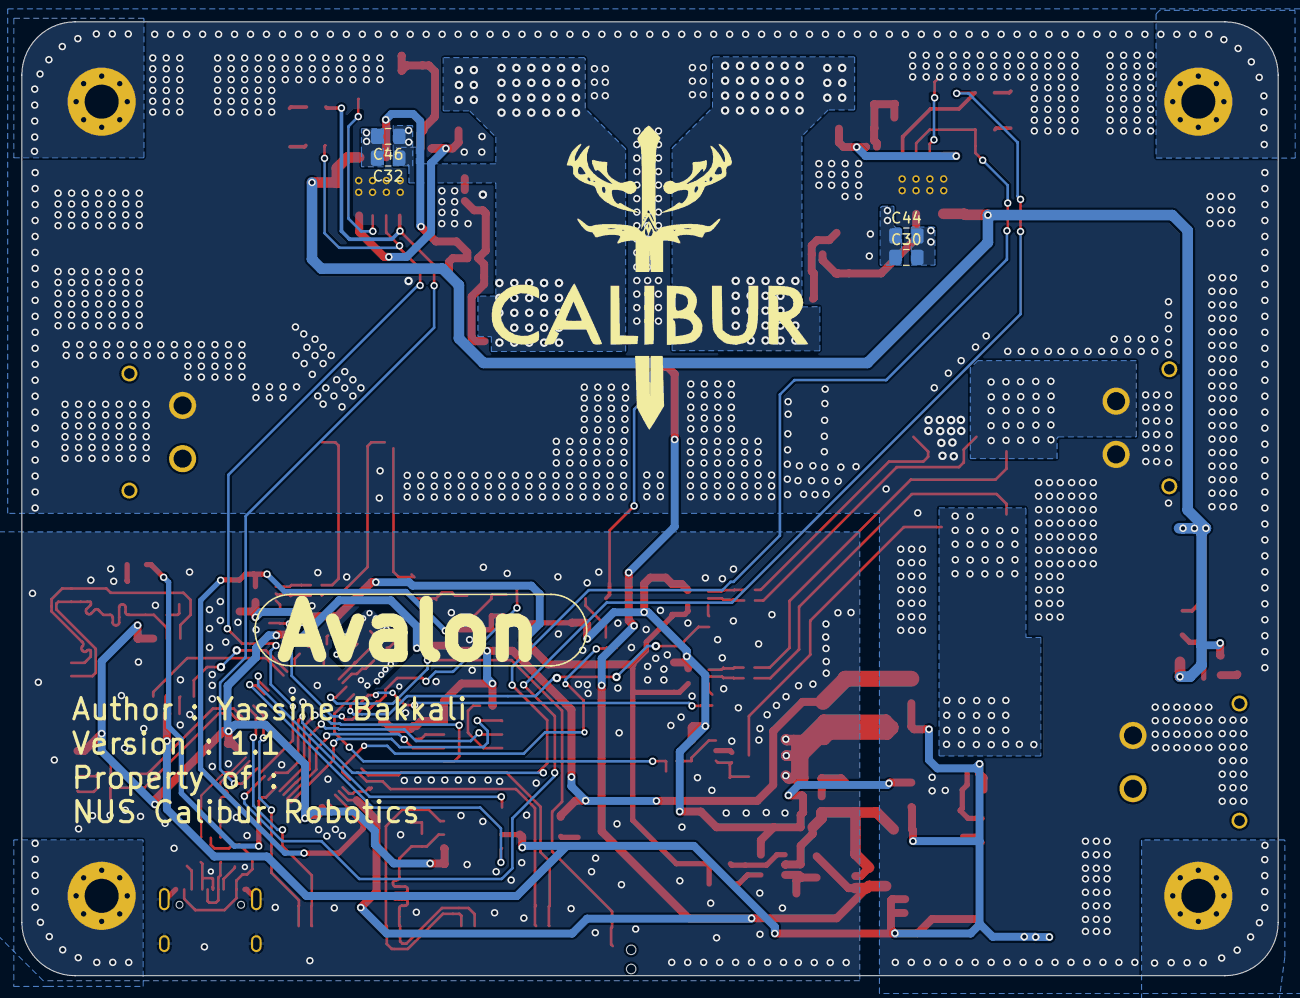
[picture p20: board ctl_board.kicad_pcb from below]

Board: 4 copper layers, 118.0 x 89.6 mm, 222 parts (4 on the bottom side), 107 nets.

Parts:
C1, C63, C66, C68: 10uF; C_0603_1608Metric_Pad1.08x0.95mm_HandSolder
C2, C33: 36v10uF; C_1206_3216Metric_Pad1.33x1.80mm_HandSolder
C3, C64: 22uF; C_0603_1608Metric_Pad1.08x0.95mm_HandSolder
C4, C29: 50v100nF; C_0603_1608Metric_Pad1.08x0.95mm_HandSolder
C5, C27: 50v100pF; C_0402_1005Metric_Pad0.74x0.62mm_HandSolder
C6, C21, C24, C34: 1uF; C_0603_1608Metric_Pad1.08x0.95mm_HandSolder
C7, C11: 12pF; C_0402_1005Metric
C8, C12, C13, C14, C15, C16, C19, C20, C22, C23, C25, C31, C61, C62, C65, C67, C69: 100nF; C_0402_1005Metric_Pad0.74x0.62mm_HandSolder
C9, C18: 1uF; C_0402_1005Metric_Pad0.74x0.62mm_HandSolder
C10: 4.7uF; C_0402_1005Metric_Pad0.74x0.62mm_HandSolder
C17: 10nF; C_0402_1005Metric_Pad0.74x0.62mm_HandSolder
C26, C28: 4.7nF; C_0402_1005Metric_Pad0.74x0.62mm_HandSolder
C30, C32: 10uF; C_0805_2012Metric_Pad1.18x1.45mm_HandSolder
C35, C70, C71, C72, C73, C74, C75, C85, C86, C87, C88, C89, C90, C91, C92, C93, C94, C95: 100nF; C_0402_1005Metric
C36, C37, C40, C41: 50v22uF; C_0805_2012Metric_Pad1.18x1.45mm_HandSolder
C43, C45: 10uF; C_1206_3216Metric_Pad1.33x1.80mm_HandSolder
C44, C46: 100nF; C_0805_2012Metric_Pad1.18x1.45mm_HandSolder
C47, C48, C49, C53, C54, C55: 220uF@35V; A769KS227M1VLAS016
C50, C51, C52, C56, C57, C58, C59, C60: 20uF@50V; C_0805_2012Metric_Pad1.18x1.45mm_HandSolder
C76, C77, C78, C79, C80, C81, C82, C83, C84: 10nF; C_0402_1005Metric
D1, D2, D5, D6, D7, D8, D13: LED; LED_0603_1608Metric_Pad1.05x0.95mm_HandSolder
D3, D4, D9, D10, D11, D12: TPD1E10B06DPYR-EV; D_0402_1005Metric_Pad0.77x0.64mm_HandSolder
D14, D15, D16, D17: MMSD4148T3G; D_SOD-123
D18, D20, D22, D23: BAT41ZFILM; D_SOD-123
D19, D21: SMCJ33A; D_SMC
F3: 0685H9300-01; Fuse_1206_3216Metric
H1, H2, H3, H9: MountingHole_Pad; MountingHole_3.2mm_M3_Pad_Via
IC2, IC8: AZ1117CH-3.3TRG1; SOT230P700X180-4N
IC3: AT25EU0021A-SSHN-T; SOIC127P600X175-8N
IC4, IC6: ATA6560-GAQW-N; SOIC127P600X175-8N
J2: MOLEX_ClikMate; Molex_PicoBlade_53261-0471_1x04-1MP_P1.25mm_Horizontal
J3: USB_C_Receptacle_USB2.0; USB_C_Receptacle_HRO_TYPE-C-31-M-12
J4: XT30PW; XT30PWM
J6, J7, J8, J9: JST_GH_SM02; JST_GH_SM02B-GHS-TB_1x02-1MP_P1.25mm_Horizontal
J13, J14: JST_GH_SM03; JST_GH_SM03B-GHS-TB_1x03-1MP_P1.25mm_Horizontal
J15, J16: XT30PW-F; XT30PWF
L1: 10.0uH; IND_VLS5045EX-100M
L2, L5: 26R@100MHz; L_0603_1608Metric_Pad1.05x0.95mm_HandSolder
L3: 3.6uH; IND_ASPI-6045S-3R6N-T
L4: 15uH; IND_SUPERCAP
Q1, Q2, Q3, Q4: POW_NMOS; DFN5&asterisk_6-8L_GFD
R1, R4: 100R; R_0402_1005Metric_Pad0.72x0.64mm_HandSolder
R2, R5: 22.1k; R_0805_2012Metric_Pad1.20x1.40mm_HandSolder
R3, R11, R13, R15, R17, R18: 200R; R_0603_1608Metric_Pad0.98x0.95mm_HandSolder
R6, R7: 5.1kR; R_0402_1005Metric_Pad0.72x0.64mm_HandSolder
R8, R19, R20, R21: 1M; R_0603_1608Metric_Pad0.98x0.95mm_HandSolder
R9, R10, R14, R16: 20k; R_0402_1005Metric
R12: 1k; R_0603_1608Metric_Pad0.98x0.95mm_HandSolder
R23, R27: 4.7k; R_0402_1005Metric_Pad0.72x0.64mm_HandSolder
R30, R31, R34, R35: 60R; R_0402_1005Metric_Pad0.72x0.64mm_HandSolder
R39: 115.8k; R_0805_2012Metric_Pad1.20x1.40mm_HandSolder
R42, R56, R57, R72: 100k; R_0805_2012Metric_Pad1.20x1.40mm_HandSolder
R43, R73, R77: 10k; R_0603_1608Metric_Pad0.98x0.95mm_HandSolder
R51: 309.0k; R_0805_2012Metric_Pad1.20x1.40mm_HandSolder
R52, R53, R54, R55: 1R; R_0402_1005Metric
R58: 1k; R_0805_2012Metric_Pad1.20x1.40mm_HandSolder
R59: 33R; R_0805_2012Metric_Pad1.20x1.40mm_HandSolder
R60, R61, R62: 0.002R; R_2512_6332Metric
R63, R64, R65, R66, R67, R68, R69, R70, R71, R74, R75, R76: 100R; R_0402_1005Metric
S1: EVQP7C01P
TH1: NTC 10K; R_0603_1608Metric_Pad0.98x0.95mm_HandSolder
U1: STM32G474RETx; LQFP-64_10x10mm_P0.5mm
U2, U8: UCC27211AQDDARQ1; DDA0008E_N
U3: USBLC6-2SC6; SOT-23-6
U4: REF3033; SOT-23
U6, U7: AP63200WU; TSOT-23-6
U9, U12, U13: INA186A2IDCKT; INA186
U11, U14, U15, U16: NCS325; SOT-23-5
Y3: ECS-480-8-33B2Q-JVY-TR3; Crystal_SMD_3225-4Pin_3.2x2.5mm
kibuzzard-6681496D: G***; kibuzzard-6681496D
kibuzzard-6681497F: G***; kibuzzard-6681497F
kibuzzard-66814953: G***; kibuzzard-66814953

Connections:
+1V65REF: C85.1, C86.1, C87.1, R58.1, R59.1, U9.1, U12.1, U13.1
+3.3VA: C17.1, C18.1, C65.1, C66.1, C70.1, C71.1, C72.1, C73.1, C74.1, C75.1, IC8.2 (OUTPUT), L2.2, U1.29 (VDDA), U9.3, U11.5 (V+), U12.3, U13.3, U14.5 (V+), U15.5 (V+), U16.5 (V+)
+3.3VREF: C8.1, C9.1, C67.1, C68.1, L5.2, R56.1, TH1.1, U1.28 (VREF+)
+3V3: C3.1, C10.1, C12.1, C13.1, C14.1, C15.1, C16.1, C23.1, C25.1, IC2.2 (OUTPUT), IC2.4 (VOUT), IC3.8 (VCC), IC4.5 (NSIL), IC6.5 (NSIL), J2.4, R11.2, R23.1, R27.2, U1.1 (VBAT), U1.16 (VDD), U1.32 (VDD), U1.48 (VDD), U1.64 (VDD)
+5VD: C1.1, C20.1, C22.1, C27.2, C36.2, C37.2, C61.1, C63.1, IC2.3 (INPUT), IC4.3 (VCC), IC6.3 (VCC), IC8.3 (INPUT), L3.2, R39.1, U4.1 (IN)
+12V: C5.2, C40.2, C41.2, C43.1, C45.1, L1.2, R12.2, R51.1, U2.1 (VDD), U8.1 (VDD)
+24V: C2.1, C33.1, F3.2, R42.2, R62.1, R68.2, U6.2 (EN), U6.3 (IN), U7.2 (EN), U7.3 (IN)
/CAN_UART INTERFACES/CAN1_+: IC4.7 (CANH), J8.2, J9.2, R30.1
/CAN_UART INTERFACES/CAN1_-: IC4.6 (CANL), J8.1, J9.1, R31.2
/CAN_UART INTERFACES/CAN3_+: IC6.7 (CANH), J6.2, J7.2, R34.1
/CAN_UART INTERFACES/CAN3_-: IC6.6 (CANL), J6.1, J7.1, R35.2
/CAN_UART INTERFACES/PB3.FDCAN3_RX: IC6.4 (RXD), U1.56 (PB3)
/CAN_UART INTERFACES/PB4.FDCAN3_TX: IC6.1 (TXD), U1.57 (PB4)
/CAN_UART INTERFACES/PB8.FDCAN1_RX: IC4.4 (RXD), U1.61 (PB8)
/CAN_UART INTERFACES/PB9.FDCAN1_TX: IC4.1 (TXD), U1.62 (PB9)
/CAN_UART INTERFACES/PC4.UART1_TX: D10.2 (K2), J14.2, U1.22 (PC4)
/CAN_UART INTERFACES/PC5.UART1_RX: D9.2 (K2), J14.3, U1.23 (PC5)
/CAN_UART INTERFACES/PC10.UART4_TX: D11.2 (K2), J13.2, U1.52 (PC10)
/CAN_UART INTERFACES/PC11.UART4_RX: D12.2 (K2), J13.3, U1.53 (PC11)
/MCU/PA0.ADC1_IN1|I_CAP_ADC: C88.1, R69.2, U1.12 (PA0)
/MCU/PA1.ADC1_IN2|V_TEMP_ADC: C94.1, R76.2, U1.25 (PB1)
/MCU/PA2.ADC1_IN3|I_CHASSIS_ADC: C90.1, R71.2, U1.11 (PC3)
/MCU/PA9.TIM1_CH3|CAP_MOS_HIGH: R3.2, U1.43 (PA9), U8.5 (HI)
/MCU/PA10.TIM1_CH2|BAT_MOS_HIGH: R15.2, U1.41 (PC9), U2.5 (HI)
/MCU/PA13.SWDIO: D3.2 (K2), R1.2, U1.49 (PA13)
/MCU/PA14.SWCLK: D4.2 (K2), R4.2, U1.50 (PA14)
/MCU/PB0.TIM1_CH2N|BAT_MOS_LOW: R17.2, U1.40 (PC8), U2.6 (LI)
/MCU/PB1.TIM1_CH3N|CAP_MOS_LOW: R13.2, U1.42 (PA8), U8.6 (LI)
/MCU/PB12.SPI2_CS: IC3.1 (~CS), U1.34 (PB12)
/MCU/PB13.SPI2_SCK: IC3.6 (SCK), U1.35 (PB13)
/MCU/PB14.SPI2_MISO: IC3.2 (SO(IO1)), U1.36 (PB14)
/MCU/PB15.SPI2_MOSI: IC3.5 (SI(IO0)), U1.37 (PB15)
/MCU/PC1.ADC2_IN7|V_CHASSIS_ADC: C92.1, R74.2, U1.9 (PC1)
/MCU/PC2.ADC2_IN8|I_SOURCE_ADC: C89.1, R70.2, U1.10 (PC2)
/MCU/PC3.ADC2_IN9|V_CAP_ADC: C93.1, R75.2, U1.13 (PA1)
/MCU/PC8.LED_DRV: R18.2, U1.38 (PC6)
/MCU/PF0.RCC_IN: C11.2, U1.5 (PF0), Y3.1
/MCU/PF1.RCC_OUT: C7.1, U1.6 (PF1), Y3.3
/MCU/PG10.RST: C31.2, S1.2 (COM_1), U1.7 (PG10)
/MCU/USB_DN: U1.45 (PA11), U3.6 (I/O1)
/MCU/USB_DP: U1.46 (PA12), U3.4 (I/O2)
/Super Capacitor Charging Gates/BOOST_DRVH: D16.1 (K), R52.2, U8.3 (HO)
/Super Capacitor Charging Gates/BOOST_DRVL: D17.1 (K), R53.2, U8.8 (LO)
/Super Capacitor Charging Gates/BOOST_SOURCE: C32.1, C46.1, D23.2 (A), L4.2, Q1.1 (D), Q4.3 (S), R10.1, U8.4 (HS)
/Super Capacitor Charging Gates/BUCK_DRVH: D15.1 (K), R55.1, U2.3 (HO)
/Super Capacitor Charging Gates/BUCK_DRVL: D14.1 (K), R54.1, U2.8 (LO)
/Super Capacitor Charging Gates/BUCK_SOURCE: C30.1, C44.1, D22.2 (A), L4.1, Q2.1 (D), Q3.3 (S), R14.1, U2.4 (HS)
/Super Capacitor Charging Gates/CHARGER_IN: C47.1, C48.1, C49.1, C50.1, C51.1, C52.1, C59.1, D21.1 (K), Q3.1 (D), R61.2, R65.1
/Super Capacitor Charging Gates/CHASSIS_OUT: J16.2, R61.1, R62.2, R66.2, R67.1
/Super Capacitor Charging Gates/I_CAP: R69.1, U9.6
/Super Capacitor Charging Gates/I_CHASSIS: R71.1, U13.6
/Super Capacitor Charging Gates/I_SOURCE: R70.1, U12.6
/Super Capacitor Charging Gates/SUPERCAP_CHG: D19.1 (K), J15.2, R60.2, R63.1
/Super Capacitor Charging Gates/SUPERCAP_IN: C53.1, C54.1, C55.1, C56.1, C57.1, C58.1, C60.1, Q4.1 (D), R60.1, R64.2, R72.2
/Super Capacitor Charging Gates/V_CAP: R75.1, U15.1, U15.4 (-)
/Super Capacitor Charging Gates/V_CHASSIS: R74.1, U14.1, U14.4 (-)
/Super Capacitor Charging Gates/V_TEMP: R76.1, U16.1, U16.4 (-)
GND: C1.2, C2.2, C3.2, C6.2, C7.2, C8.2, C9.2, C10.2, C11.1, C12.2, C13.2, C14.2, C15.2, C16.2, C17.2, C18.2, C19.2, C20.2, C21.2, C22.2, C23.2, C24.2, C25.2, C26.2, C28.2, C31.1, C33.2, C34.2, C35.1, C36.1, C37.1, C40.1, C41.1, C43.2, C45.2, C47.2, C48.2, C49.2, C50.2, C51.2, C52.2, C53.2, C54.2, C55.2, C56.2, C57.2, C58.2, C59.2, C60.2, C61.2, C62.2, C63.2, C64.2, C65.2, C66.2, C67.2, C68.2, C70.2, C71.2, C72.2, C73.2, C74.2, C75.2, C79.1, C80.2, C81.2, C82.1, C83.2, C84.1, C85.2, C86.2, C87.2, C88.2, C89.2, C90.2, C91.1, C92.2, C93.2, C94.2, C95.1, D1.1 (K), D2.1 (K), D3.1 (K1), D4.1 (K1), D5.1 (K), D6.1 (K), D7.1 (K), D8.1 (K), D9.1 (K1), D10.1 (K1), D11.1 (K1), D12.1 (K1), D13.1 (K), D18.2 (A), D19.2 (A), D20.2 (A), D21.2 (A), IC2.1 (ADJ/GND), IC3.4 (GND), IC4.2 (GND), IC4.8 (STBY), IC6.2 (GND), IC6.8 (STBY), IC8.1 (ADJ/GND), J2.3, J3.A1 (GND), J3.A12 (GND), J3.B1 (GND), J3.B12 (GND), J3.S1 (SHIELD), J4.2, J13.1, J14.1, J15.1, J16.1, Q1.3 (S), Q2.3 (S), R2.2, R5.2, R6.1, R7.1, R8.1, R9.1, R16.1, R19.1, R20.1, R21.1, R43.1, R57.2, R73.1, R77.1, S1.1 (NO_1), U1.15 (VSS), U1.27 (VSSA), U1.31 (VSS), U1.47 (VSS), U1.63 (VSS), U2.7 (VSS), U2.9 (PAD), U3.2 (GND), U4.3 (GND), U6.4 (GND), U7.4 (GND), U8.7 (VSS), U8.9 (PAD), U9.2, U11.2 (V-), U12.2, U13.2, U14.2 (V-), U15.2 (V-), U16.2 (V-), Y3.2, Y3.4
unnamed: C6.1, H1.1, R19.2
unnamed: C21.1, H2.1, R20.2
unnamed: C24.1, H3.1, R21.2
unnamed: C26.1, R30.2, R31.1
unnamed: C28.1, R34.2, R35.1
unnamed: C34.1, H9.1, R8.2
unnamed: C69.1, R59.2, U11.1
unnamed: C76.1, C84.2, R68.1, U13.5
unnamed: C76.2, C83.1, R67.2, U13.4
unnamed: C77.1, C82.2, R66.1, U12.5
unnamed: C77.2, C81.1, R65.2, U12.4
unnamed: C78.1, C79.2, R64.1, U9.5
unnamed: C78.2, C80.1, R63.2, U9.4
unnamed: D1.2 (A), R3.1
unnamed: D2.2 (A), R13.1
unnamed: D5.2 (A), R11.1
unnamed: D6.2 (A), R12.1
unnamed: D7.2 (A), R15.1
unnamed: D8.2 (A), R17.1
unnamed: D13.2 (A), R18.1
unnamed: D14.2 (A), D18.1 (K), Q2.2 (G), R16.2, R54.2
unnamed: D15.2 (A), D22.1 (K), Q3.2 (G), R14.2, R55.2
unnamed: D16.2 (A), D23.1 (K), Q4.2 (G), R10.2, R52.1
unnamed: D17.2 (A), D20.1 (K), Q1.2 (G), R9.2, R53.1
unnamed: F3.1, J4.1
unnamed: IC3.7 (~HOLD/~RESET(IO3)), R27.1
unnamed: IC3.3 (~WP(IO2)), R23.2
unnamed: C64.1, IC8.4 (VOUT), L2.1
unnamed: J2.1, R1.1
unnamed: J2.2, R4.1
unnamed: J3.A5 (CC1), R6.2
unnamed: J3.B5 (CC2), R7.2
unnamed: J3.A6 (D+), J3.B6 (D+), U3.3 (I/O2)
unnamed: J3.A7 (D-), J3.B7 (D-), U3.1 (I/O1)
unnamed: C30.2, C44.2, U2.2 (HB)
unnamed: J3.A4 (VBUS), J3.A9 (VBUS), J3.B4 (VBUS), J3.B9 (VBUS), U3.5 (VBUS)
unnamed: C62.1, L5.1, U4.2 (OUT)
unnamed: C4.1, U6.6 (BST)
unnamed: C5.1, R2.1, R51.2, U6.1 (FB)
unnamed: C4.2, L1.1, U6.5 (SW)
unnamed: C29.1, U7.6 (BST)
unnamed: C27.1, R5.1, R39.2, U7.1 (FB)
unnamed: C29.2, L3.1, U7.5 (SW)
unnamed: C32.2, C46.2, U8.2 (HB)
unnamed: C19.1, R56.2, R57.1, U11.3 (+)
unnamed: C69.2, R58.2, U11.4 (-)
unnamed: C35.2, R42.1, R43.2, U14.3 (+)
unnamed: C91.2, R72.1, R73.2, U15.3 (+)
unnamed: C95.2, R77.2, TH1.2, U16.3 (+)

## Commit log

2025-04-23 Repo setup
    [buzzer_led.kicad_sch, comms.kicad_sch, ctl_board.csv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]
2025-04-23 Renamed files, threw out garbage
    [ctl_board.kicad_sch, ctl_board_bom.xlsb.csv, imu.kicad_sch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]
